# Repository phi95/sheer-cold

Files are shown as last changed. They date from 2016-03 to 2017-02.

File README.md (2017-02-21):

# SheerCold
Freeze your drinks instantly!

This is our project for GSU 2016 Hackathon.

Members:
 - Phi Long Nguyen
 - Khoa Ngo
 - Nghia Le
 - Justin Tumale
 - Dustin Nguyen

## How we came up with the idea?
Well, we all sat down and thought of a problem that we all have and that it is within
our powers to solve it. We concluded that one of the most annoying problem we have is
drinking beers that aren't cold enough. Sometimes after buying a pack, we forgot to put
them in the fridge or the ones we bought aren't cold enough and we really hated waiting
on them to get cold. So we thought it would be cool (no pun intended) to make a machine
that can instantly cool our drinks. Of course we could not work on the actual machine
before hackathon so we made a list of items to bring before hand and also worked on the
design and brought everything with us to assemble.

## Concepts
To create this project we utilized concepts of thermodynamics, heat transfer, electrical
circuits, and material design. The centerpiece of this project is the Peltier module. How
the Peltier module work is that it creates a temperature difference by transferring heat
between two electrical junctions. When current flows through the junctions, heat is removed
from one junction and transferred to the other junction, creating a cooling effect.

These are the designs we came up with:
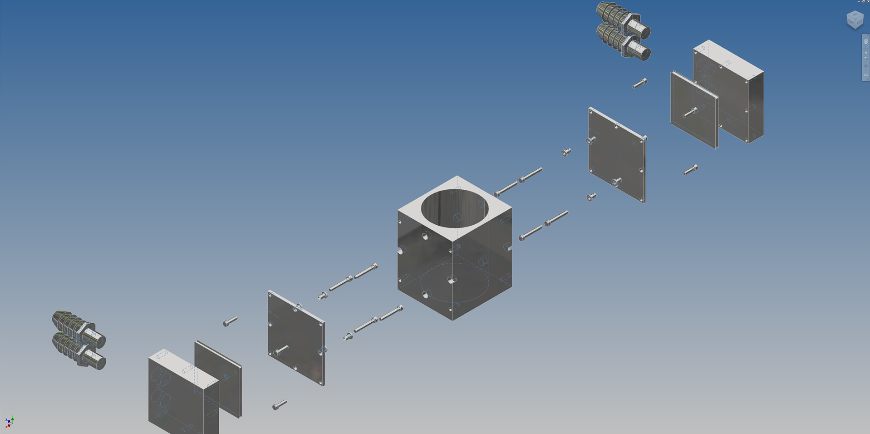
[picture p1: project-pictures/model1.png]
model1

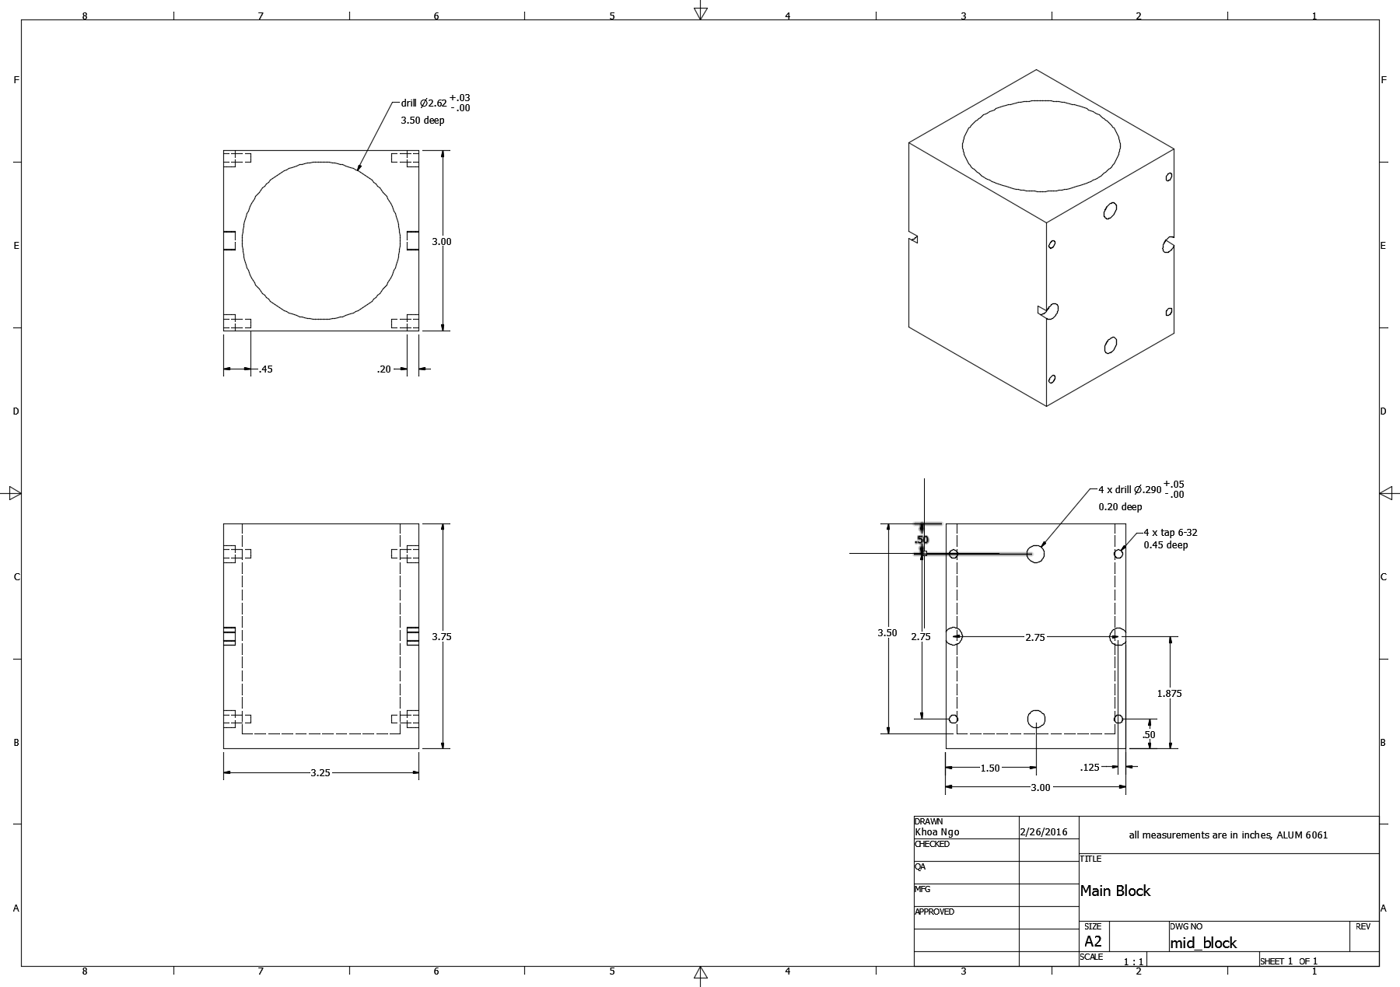
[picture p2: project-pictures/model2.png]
model2

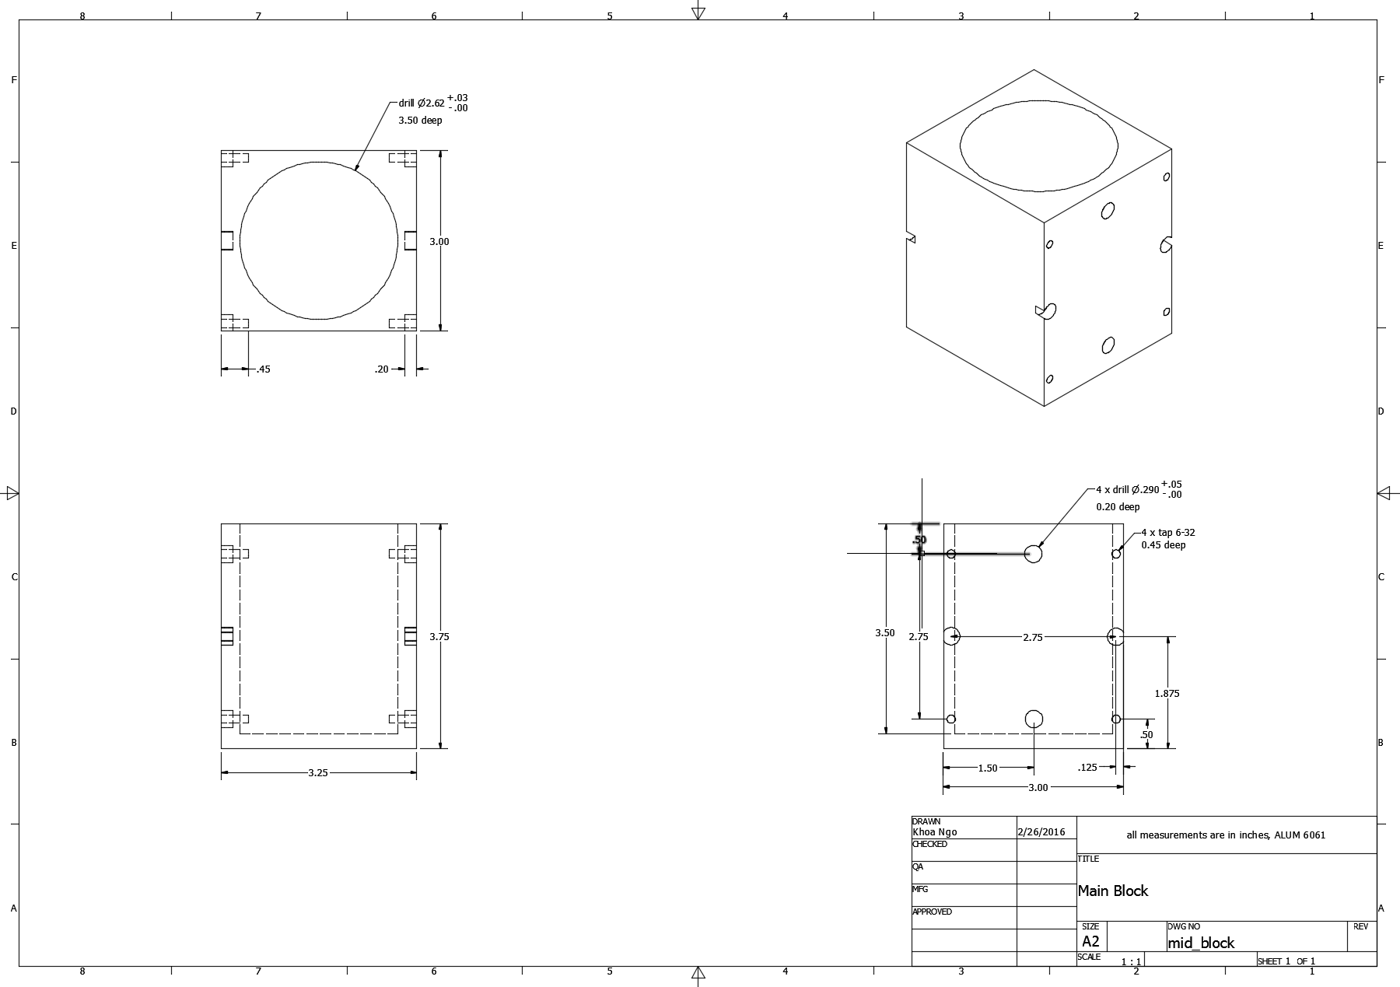
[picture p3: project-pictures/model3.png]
model3


## Materials
 - Peltier module (x2)
 - Power cords (x2)
 - Power supply (x2)
 - Thermal paste (x1)
 - Water block (x2)
 - Cold plate mounting (x2)
 - Reservoir (x1)
 - Pump (x1)
 - Aluminum encasement (x1)
 - Radiator (x1)
 - Cooling fans (x3)

## How we did it?
Before the hackathon, we 3D printed the aluminum encasement which perfectly fits a standard sized canned drink. The cold plate and the water block sandwiched the Peltier module, with the cold plate facing the aluminum casing. To manage overheating, we applied thermal paste between the Peltier module and the water block. The water block draws heat from the casing and deposits it towards the water loop, which utilizes a radiator to finally expel heat from the system. A 1000 watt power supply connects to the water cooling system, and must be manually switched on before the system may operate.
We used acrylic glass to be a part of our machine's structure.

We programmed an Arduino with sensors to read temperatures of the aluminum casing and broadcast it
onto a computer software we wrote using Python. The Python program included logos and designs we
handmade during the hackathon, an alarm that would ring when the aluminum casing reaches a set amount
of degrees, and a visual graph that allows us to see through time the temperature drop as the machine
is running.

## Problems we encountered
 1. While working on this project we had problems with the water cooling mechanism.
 We realized that the placement of the reservoir matters. We had placed it below the pump
 and water would not pump, due to gravity having a greater force than the pump itself. After
 many trial-and-errors we learned that having the reservoir above the pump allowed water to flow.

 2. This one isn't so much a problem we encountered but rather a design flaw. We realized that
 to run this machine would require a tremendous amount of energy, needing two power supplies.

 3. This one is a software problem that we had. To most of us, we are using completely new software
 along with new hardware. Most of us are learning a new language as well as playing with some new
 hardware so there was definitely a learning curve during the first half of hackathon.

 4. We realized after we finished building the machine that we did not bring a voltage checker,
 therefore we were not able to fine tune the power supply to its optimal level.

## Award
We were awarded best hardware hack.
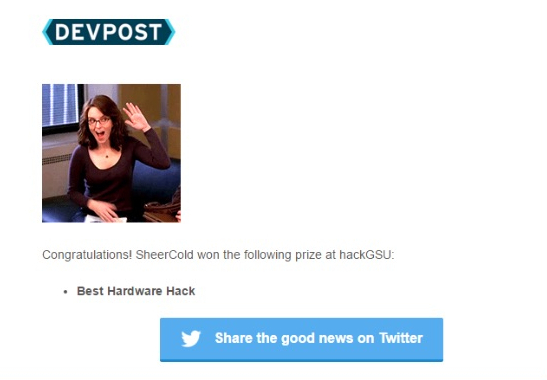
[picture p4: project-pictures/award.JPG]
award


## The Process
These are pictures of use tuning the machine
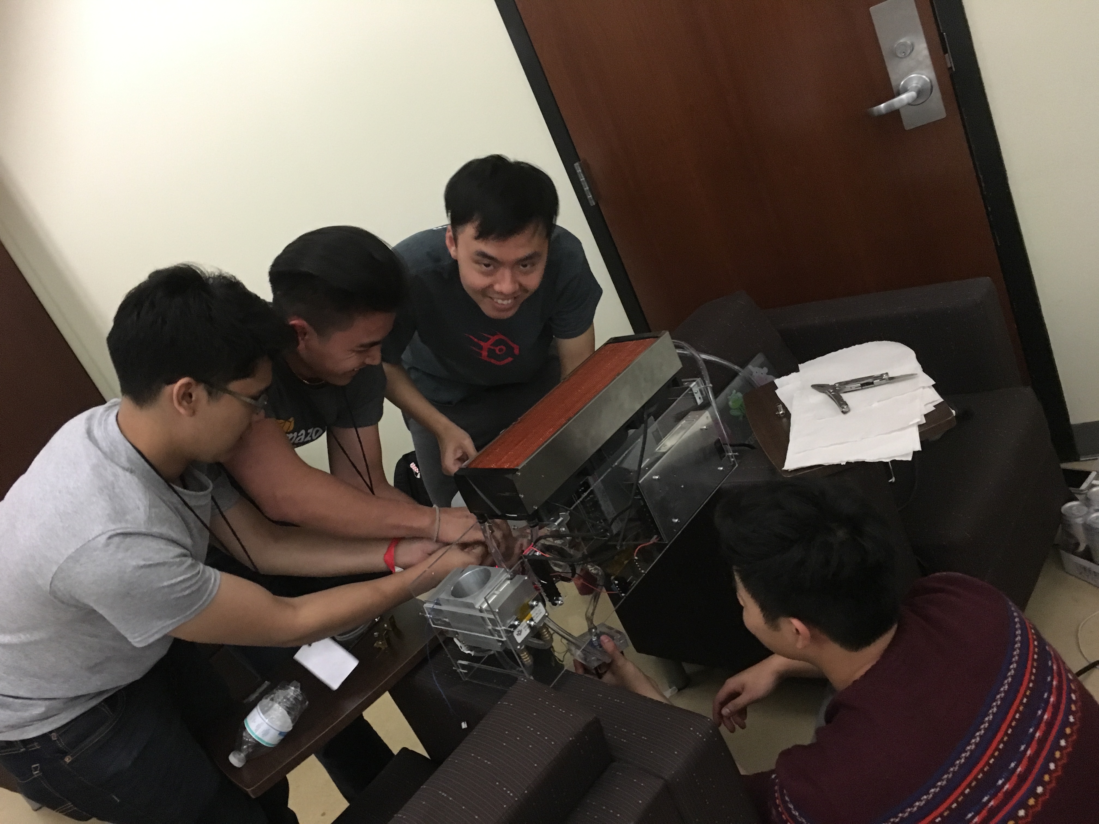
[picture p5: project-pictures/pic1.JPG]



Here we are taking a break at a local pho restaurant
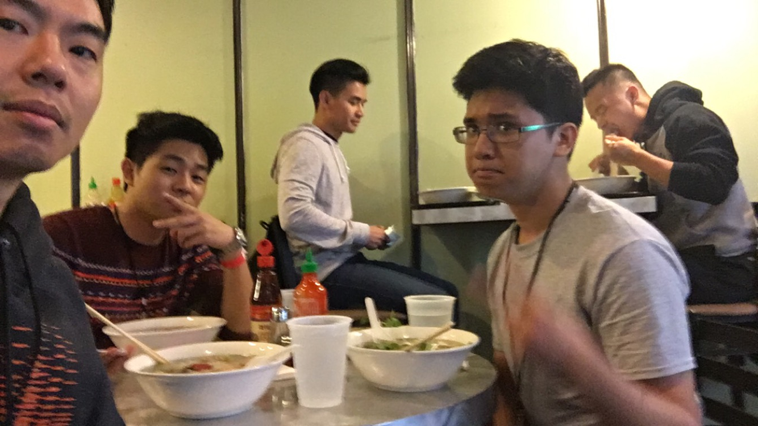
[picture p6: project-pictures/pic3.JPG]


Here is the finish document ready to be presented
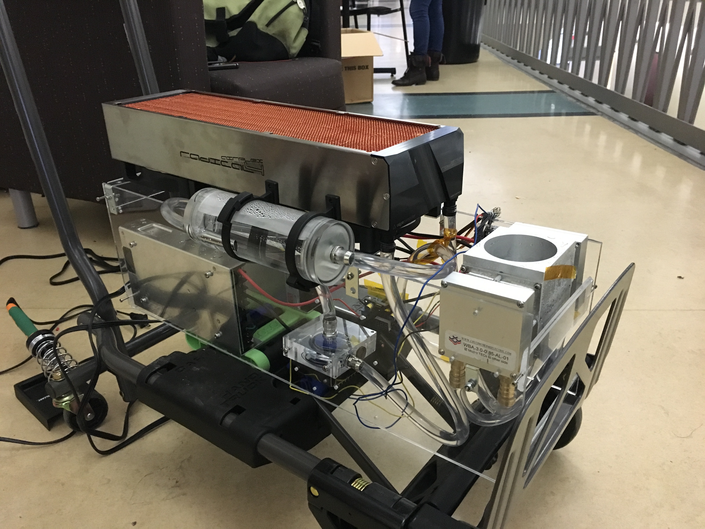
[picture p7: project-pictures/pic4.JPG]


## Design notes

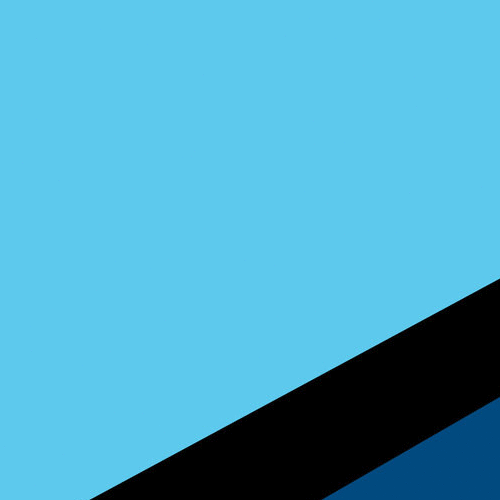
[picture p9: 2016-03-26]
images/mblue.gif

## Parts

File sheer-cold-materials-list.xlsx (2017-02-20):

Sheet: Part List
Quantity | Type | Part | Cost per unit | Total cost | Supplier | Documents | Note
2 | Peltier module | TEC1-12730S | $32.19 | $64.38 | peltiermodules (http://peltiermodules.com/?p=product) |  | Sealed
2 | Power cords | PSC-5-15-10A-1.83 | $6.25 | $12.50 | customthermoelectric (http://www.shop.customthermoelectric.com/AC-Power-Cord-6-long-PSC-5-15-10A-183.htm)
2 | Power supply | 709-SE600-15 | $91.13 | $182.26 | mouser (http://www.mouser.com/ProductDetail/Mean-Well/SE-600-15/?qs=sGAEpiMZZMsPs3th5F8koBOlc8SUmHBQshmGtzD1r8s%3d)
1 | Thermal sheet | TS-MFA4 | $7.50 | $7.50 | customthermoelectric (http://www.shop.customthermoelectric.com/Thermal-Sheet-TS-MFA4-TS-MFA4.htm)
2 | Water block | WBA-3.0-0.85-AL-R2 | $87.50 | $175.00 | customthermoelectric (http://www.shop.customthermoelectric.com/Water-Block-30-x-30-x-085-WBA-30-085-AL-R2.htm)
2 | Cold plate | CPT-3.0-3.0-0.25-AL | $0.00 | $0.00 | customthermoelectric (http://www.shop.customthermoelectric.com/Cold-Plate-w-Mounting-holes-30-x-30-x-025-CPT-30-30-025-AL.htm)
1 | Resevoir | Swiftech MCRES | $24.95 | $24.95 | performance-pcs (http://www.performance-pcs.com/swiftech-mcres-micro-rev-2-reservoir.html)
1 | Pump | Alphacool Laing DDC310 | $74.94 | $74.94 | performance-pcs (http://www.performance-pcs.com/pumps/alphacool-laing-ddc310-complete-edition-plata-plexi.html)
1 | Radiator | Aquacomputer 420 copper | $157.99 | $157.99 | performance-pcs (http://www.performance-pcs.com/aquacomputer-airplex-radical-4-420-copper-fins.html)
1 | Aluminium encasement | Custom | $0.00 | $0.00 | N/A
 |  |  | Total cost | $699.52

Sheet: Peltier Modules
Quantity | Part | Cost per unit | Total cost | Supplier | Imax | Vmax | Wmax | Q (@dT=30) | TotalQ (@dt=30) | Qmax (@30C) | A (mm) | B (mm) | H (mm) | Note
2 | HP-199-1.4-0.8 | $39.10 | $78.20 | tetech (http://tetech.com/product/hp-199-1-4-0-8/) | 11.3 | 24.6 | 277.98 | 73 | 146 | 130 | 40 | 40 | 3.2 | Potted
1 | 19911-5M31-28CZ | $56.50 | $56.50 | customthermoelectric (http://www.shop.customthermoelectric.com/19911-5M31-28CZ-Thermoelectric-Peltier-Module-19911-5M31-28CZ.htm;jsessionid=B9A34EB21D74D02EA9EA4B723ED155FE.m1plqsc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) | 28 | 24.8 | 694.4 | 200 | 200 | 400 | 62 | 62 | 3.3
2 | TEC1-12730 | $32.19 | $64.38 | peltiermodules (http://peltiermodules.com/?p=product) | 30.5 | 15.6 | 475.8 | 147 | 294 | 260 | 62 | 62 | 3.9

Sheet: Power Supply
Quantity | Part | Cost per unit | Total cost | Supplier | I rated | V | W rated | deltaI | deltaV | deltaW | Peltier+PS cost | Peltier+PS total cost | W/total cost
2 | 709-MSP300-24 | $64.25 | $128.50 | mouser (http://www.mouser.com/ProductDetail/Mean-Well/EPP-300-24/?qs=sGAEpiMZZMsPs3th5F8koELBKcKbsI6WdbGOCAN1ecM%3d) | 12.5 | 24 | 300 | 1.2 | -0.6 | 22.02 | $103.35 | $206.70 | 0.706
1 | 709-RSP750-24 | $181.63 | $181.63 | mouser (http://www.mouser.com/ProductDetail/Mean-Well/RSP-750-24/?qs=21bV%2fTPs%2bw8UMO2dEhMdnQ%3d%3d) | 31.3 | 24 | 751.2 | 3.3 | -0.8 | 56.8 | $238.13 | $238.13 | 0.840
2 | 709-SE600-15 | $91.13 | $182.26 | mouser (http://www.mouser.com/ProductDetail/Mean-Well/SE-600-15/?qs=sGAEpiMZZMsPs3th5F8koBOlc8SUmHBQshmGtzD1r8s%3d) | 40 | 15 | 600 | 9.5 | -0.6 | 124.2 | $123.32 | $246.64 | 1.192

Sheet: Rough Calculation
item | mass (g) | specific heat (J/g* C) | heat capacity (J/ C)
water | 355 | 4.179 | 1483.545
aluminium can | 16.55 | 0.902 | 14.93
delta T ( C) | 16 |  |  | water heat of fusion (J/g) | 334
delta E (J) | 23975.57 |  |  | mass of water | 1.1746
delta E (Wh) | 6.66 |  |  | E_fusion | 392.3164
 |  |  |  | % of total E (%) | 1.636317329
Qc (W) | time (m)
100 | 3.996
150 | 2.664
200 | 1.998
250 | 1.598
300 | 1.332
350 | 1.142
400 | 0.999
450 | 0.888
500 | 0.799
550 | 0.727
600 | 0.666
650 | 0.615
700 | 0.571
750 | 0.533
Thermal properties | specific heat (J/kg* C) | thermal conductivity (W/m*K) | freezing point( C)
Copper | 385 | 385 | N/A
Aluminium | 897 | 205 | N/A
Ice | 2027 | 2.25 | N/A
Water | 4182 | 0.609 | 0
Alcohol, ethyl | 2440 | 0.171 | -114
Neoprene | N/A | 0.09 | N/A
styrofoam | N/A | 0.033 | N/A
Air | 1005 | 0.024 | -217
Aerogel blanket | N/A | 0.023 | N/A

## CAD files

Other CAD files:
AutoCAD Designs/CAD/mid_block.dwg
AutoCAD Designs/CAD/center_piece_exploded.dwg
AutoCAD Designs/CAD/cold_plate.dwg
AutoCAD Designs/CAD/center_piece.iam
AutoCAD Designs/CAD/cold_plate.ipt
AutoCAD Designs/CAD/mid_block.ipt
AutoCAD Designs/CAD/peltier_module.ipt
AutoCAD Designs/CAD/shoulder_washer_plate.ipt
AutoCAD Designs/CAD/water_block_top.ipt

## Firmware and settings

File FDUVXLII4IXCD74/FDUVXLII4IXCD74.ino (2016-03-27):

#include <max6675.h>


// ThermoCouple
int thermo_gnd_pin = 7;
int thermo_vcc_pin = 6;
int thermo_so_pin  = 5;
int thermo_cs_pin  = 4;
int thermo_sck_pin = 3;
String reader;
char c;
  
MAX6675 thermocouple(thermo_sck_pin, thermo_cs_pin, thermo_so_pin);
  
void setup() {
  Serial.begin(9600);

  pinMode(thermo_vcc_pin, OUTPUT); 
  pinMode(thermo_gnd_pin, OUTPUT); 
  digitalWrite(thermo_vcc_pin, HIGH);
  digitalWrite(thermo_gnd_pin, LOW);
}

void loop() {
  
  while (Serial.available()){
    if (Serial.available() > 0){
      c = Serial.read();
      reader += c;
      //Serial.println(reader + "&");
    };
  }
  if (reader.length() > 0){
    Serial.println(reader + "&");
    reader = "";
  };
  
  Serial.println(thermocouple.readCelsius()-5);
  delay(1000);
}

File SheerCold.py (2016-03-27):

#!/usr/bin/python
import serial #Import Serial Library
from tkinter import *
import tkinter as tk
from time import sleep
import simpleaudio as sa


root = tk.Tk()
graphOn = False
currentTemp = 0
setTemp = 0
checkTemp = False
loop = True

var = StringVar()
degreesText = " C"
#arduinoSerialData = serial.Serial('/dev/cu.usbmodemFD121', 9600) #object...tell it which COMPORT are you on?
#arduinoSerialData = serial.Serial('COM4', 9600) #object...tell it which COMPORT are you on?
arduinoSerialData = serial.Serial('/dev/cu.usbmodem411', 9600)


#initialize the graph

'''
backgroundPicGraph = PhotoImage(file = "images/graphBlue.gif")
backgroundGraph = Label(root, image = backgroundPicGraph)
'''
#backgroundGraph.image = backgroundPicGraph #reference
#backgroundGraph.pack()


def setCurrentTemp(x):
	global currentTemp
	currentTemp = x

def getCurrentTemp():
	global currentTemp
	return currentTemp

def setSetTemp(x):
	global setTemp
	setTemp = x

def getSetTemp():
	global setTemp
	return setTemp

def update():

	count = 0
	time_count = 0

	graph_file_buffer = [None]*3		#initialize the output buffer
	graph_file_buffer[1] = ','			#place comma for formatting

	while loop:


		graph_file_buffer[0] = str(time_count)
		time_count += 1							#keep track of the time to write to a file for graphing

		line = arduinoSerialData.readline()
		line = line.decode('utf-8')
		global checkTemp
		if checkTemp:
			if getCurrentTemp() < getSetTemp():
				playAlarm()
				print("The temperature is below", getSetTemp(), "degrees Celsius. ")
				checkTemp = False

		if '&' in line:
			line = str(line)
			line = line.replace("&","")
			line = int(line)
			print("Setting temperature to below", str(line), "degrees Celsius...")
			root.update()

		else:
			#update graph
			count += 1

			#update the temperature display
			line = line.replace('\n', '').replace('\r', '')
			setCurrentTemp(float(line))
			var.set(line + degreesText)

			graph_file_buffer[2] = str(line)	#initialize buffer
			write_to_file(graph_file_buffer)	#write the the output to a text file for graphing
			clear_buffer(graph_file_buffer)		#clear the buffer

			root.update()
			sleep(1)

def write_to_file(graph_file_buffer):
	target = open('plot.txt', 'a')

	output = ""
	for i in graph_file_buffer:
		output += i

	target.write(output+'\n')
	target.close()



def clear_buffer(graph_file_buffer):
	graph_file_buffer[0] = ""
	graph_file_buffer[2] = ""

def set_temperature():
	global checkTemp
	setTemp = entry.get()
	checkTemp = True
	#print("Setting temperature to", setTemp , "...")
	setTemp = setTemp.encode('utf-8')
	arduinoSerialData.write(setTemp)
	setSetTemp(float(setTemp))

def playAlarm():
    wave_obj = sa.WaveObject.from_wave_file("beep.wav")
    play_obj = wave_obj.play()
    play_obj.wait_done()


def quit():
	global loop
	loop = False
	sys.exit(0)



#background
backgroundPic = PhotoImage(file = "images/mblue.gif")
background = Label(root, image = backgroundPic)
background.image = backgroundPic #reference
background.pack()

#Setting the logo
logoPic = PhotoImage(file = "images/logo.gif")
logo = Label(root, image=logoPic)
logo.image = logoPic #reference
logo.place(x = 0, y = 0)

#Label that prints the degrees
label = Label(root, textvariable = var, fg = 'white', bg = 'black', font = ("Times", 40))
label.place(relx=.5, anchor = CENTER, y = 130)

#Set temp label
setTempText = Label(root, text="Set Temperature: ", fg = 'white', bg = 'black', font = ("Times", 15))
setTempText.place(relx = .28, anchor = CENTER, y = 250)

#create entry form
entry = Entry(root, bg = 'black', fg = 'white', font = ("Times", 15))
entry.place(relx = .6, anchor = CENTER, y = 250)

button = Button(root, text="Enter", command=set_temperature)
button.configure(bg = 'black')
button.place(relx = .5, anchor = CENTER, y = 300)

button2 = Button(root, text=" Quit  ", command=quit)
button2.configure(bg = 'black')
button2.place(relx = .70, anchor = CENTER, y = 300)


root.after(1,update)
root.mainloop()

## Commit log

2016-03-26 added the Arduino output and the serial receiver files
2016-03-26 gui can read data from arduino
2016-03-26 added separate frames to the user interface
2016-03-26 Fixed layout format in SheerCold.py syntax error in Sound.py
    [SheerCold.py]
2016-03-26 Output now being sent to Arduino
2016-03-26 Arduino reading inputs and sending confirmation output back to Python
2016-03-26 GUI
    Converted mblue into proper gif, image can be used in GUI via canvas but
    there are issues with label placement.
    [SheerCold.py]
2016-03-26 fixed formating a little
    [SheerCold.py]
2016-03-26 temperature comparisons
2016-03-26 working on setting temperature
2016-03-26 global stuff trying to fix
    [SheerCold.py]
2016-03-26 fixed int decode error
    [SheerCold.py]
2016-03-27 Fahrenheit ----> Celsius (Arduino)
2017-02-20 updated readme and added design files
    [center_piece.iam, center_piece_exploded.dwg, cold_plate.dwg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]
